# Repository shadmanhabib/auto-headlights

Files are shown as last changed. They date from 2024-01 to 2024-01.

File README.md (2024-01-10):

# Auto-Headlights
Controller designed to control and automate vehicle headlights based on environmental conditions in parallel with vehicle controls.

## Table of Contents
- [Auto-Headlights](#Auto-Headlights)
  - [Table of Contents](#table-of-contents)
  - [About The Project](#about-the-project)
  - [Getting Started](#getting-started)
    - [Prerequisites](#prerequisites)
    - [Installation](#installation)
  - [Usage](#usage)
  - [Changelog](#changelog)

## About The Project
This project was designed for a Subaru Liberty/Legacy 4GEN in an effort to add modern automatic headlights and light home functionalities.

It involves PCB design and automotive wiring. Hence, this project should only be replicated by individuals who are confident with automotive electrical systems.

The design was based around the following requirements:

1. Control headlights dependent on light conditions.
2. Ensure original vehicle controls remained functional.
3. Support reading lock/unlock states.
4. Ability to update software i.e. ensure programing pins are accessible through header/connector.

## Getting Started
To get a build this project (or parts thereof), these steps may be followed.

### Prerequisites
1. PlatformIO is required to build binaries from source code. Microchip Studios or Arduino IDE can also be used but will require extra configuration.
2. An ISP programmer is required to upload to the controller. An Arduino as ISP can be used.
3. If you want to make changes to the PCB design or would like to generate new fabrication files, an installation of KiCAD is required.
4. A 3D printer is required to fabricate the PCB enclosure from the provided CAD files.

### Installation
1. Manufacture and assemble controller PCB.
2. Build and upload code binary.
3. Fabricate PCB enclosure.
4. Splice vehicle wiring as per wiring diragram/requirements.
5. Pin connectors and attach to controller.
6. Mount controller in a secure location.

## Usage
Examples will be given in future iterations of this file.

_For more examples, please refer to the [Documentation](https://)_

## Changelog
All notable changes to this project will be documented in this section.

The format is based on [Keep a Changelog](https://keepachangelog.com/en/1.0.0/),
and this project attempts to adhere to [Semantic Versioning](https://semver.org/spec/v2.0.0.html).

### [v1.0.0]
#### Initial design
- ATmega328PB based design.
- Included optocouplers to read 12V signals from vehicle.
- MOLEX Micro-fit connectors.

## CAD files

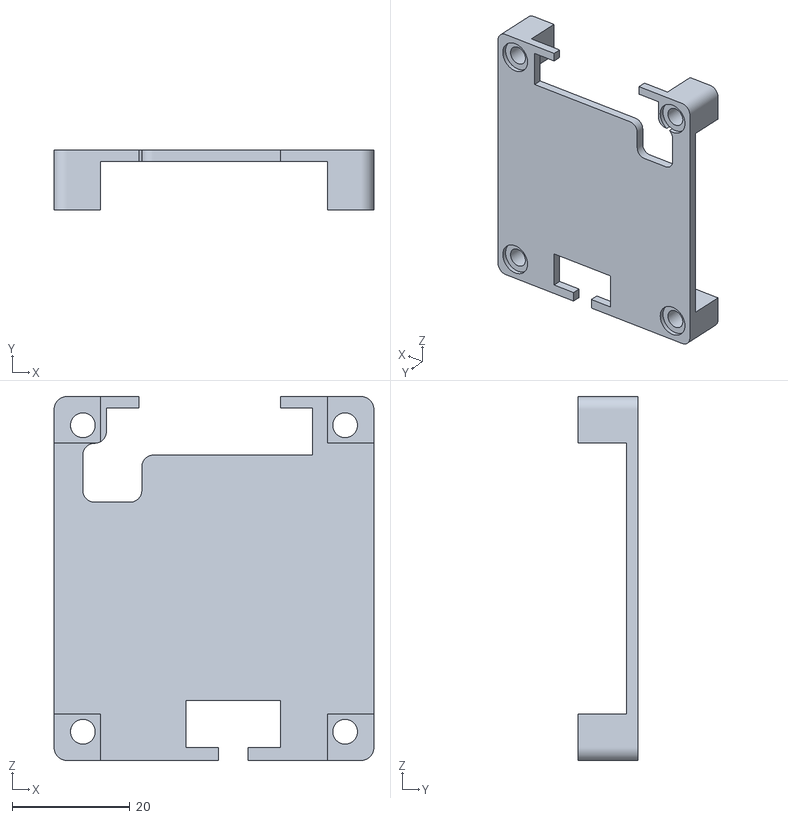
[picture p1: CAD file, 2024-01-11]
CAD/export/lid.obj
54.3 x 10.2 x 61.8

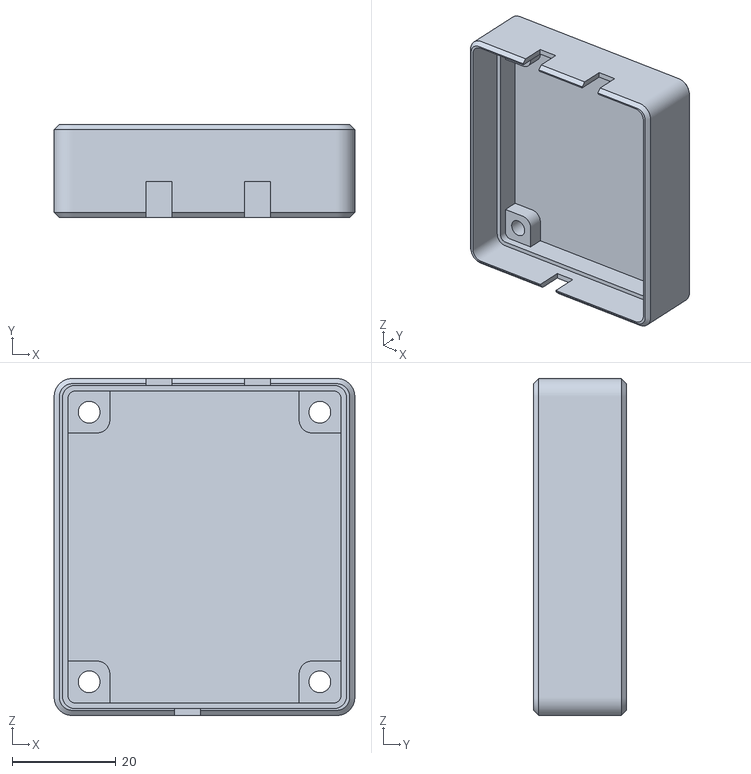
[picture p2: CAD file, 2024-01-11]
CAD/export/case.obj
58.0 x 18.0 x 65.0

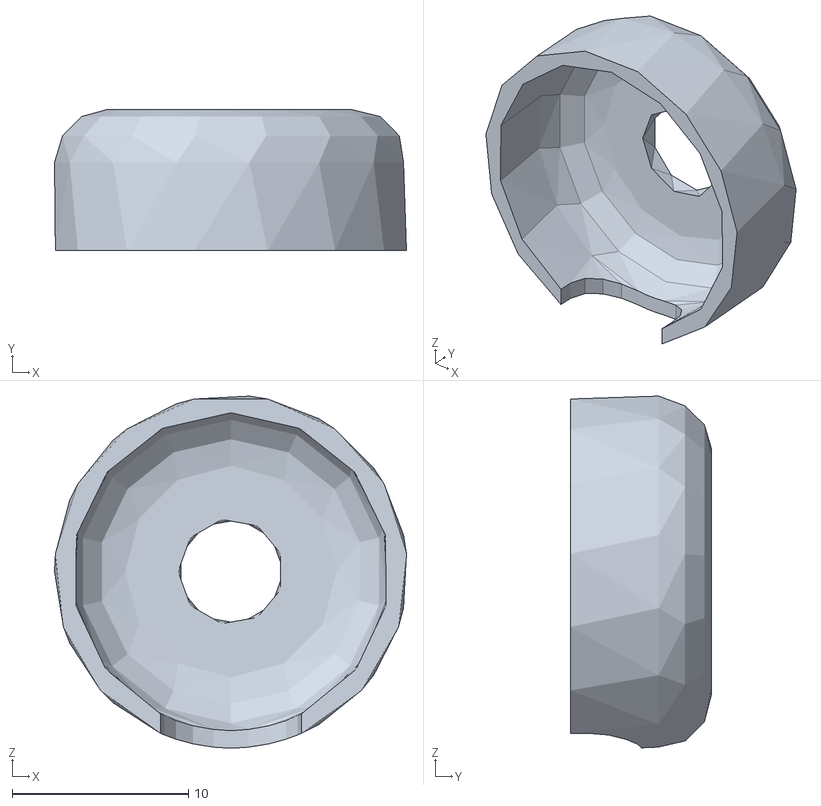
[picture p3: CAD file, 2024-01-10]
CAD/export/Light_sensor_case.obj
19.9 x 8.00 x 19.9

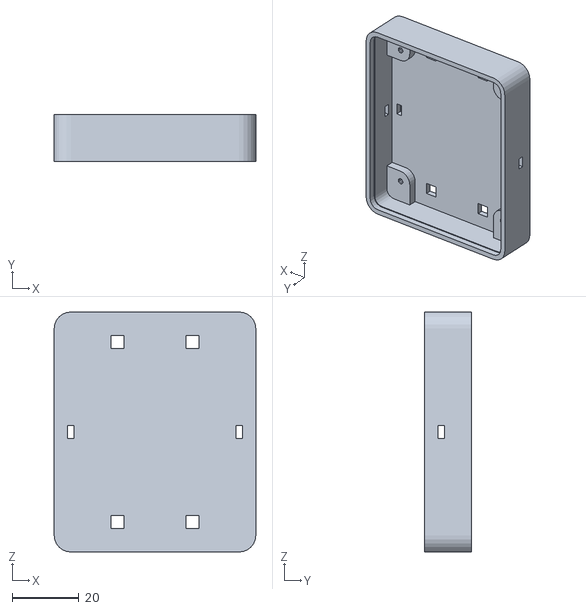
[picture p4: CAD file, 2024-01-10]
CAD/export/PCB_case_1.obj
60.5 x 14.0 x 72.0

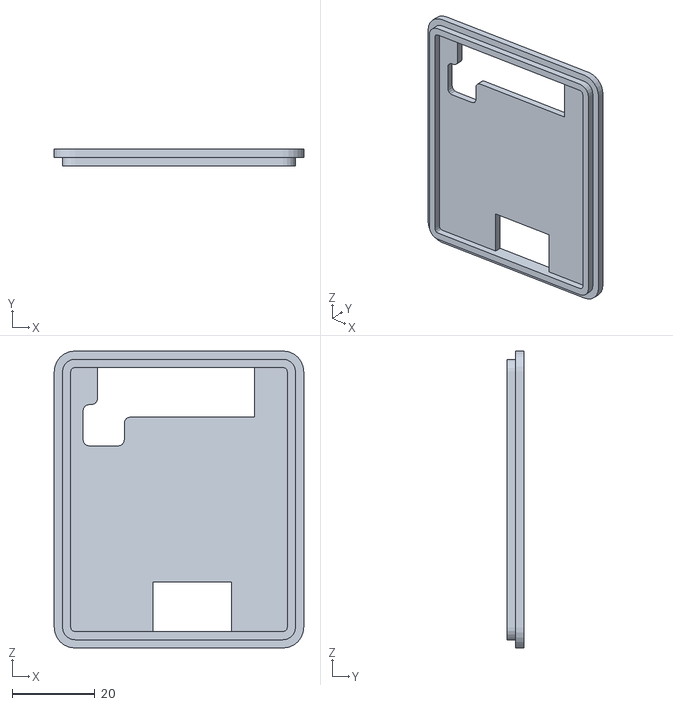
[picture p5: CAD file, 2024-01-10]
CAD/export/PCB_case_2.obj
60.5 x 4.00 x 72.0

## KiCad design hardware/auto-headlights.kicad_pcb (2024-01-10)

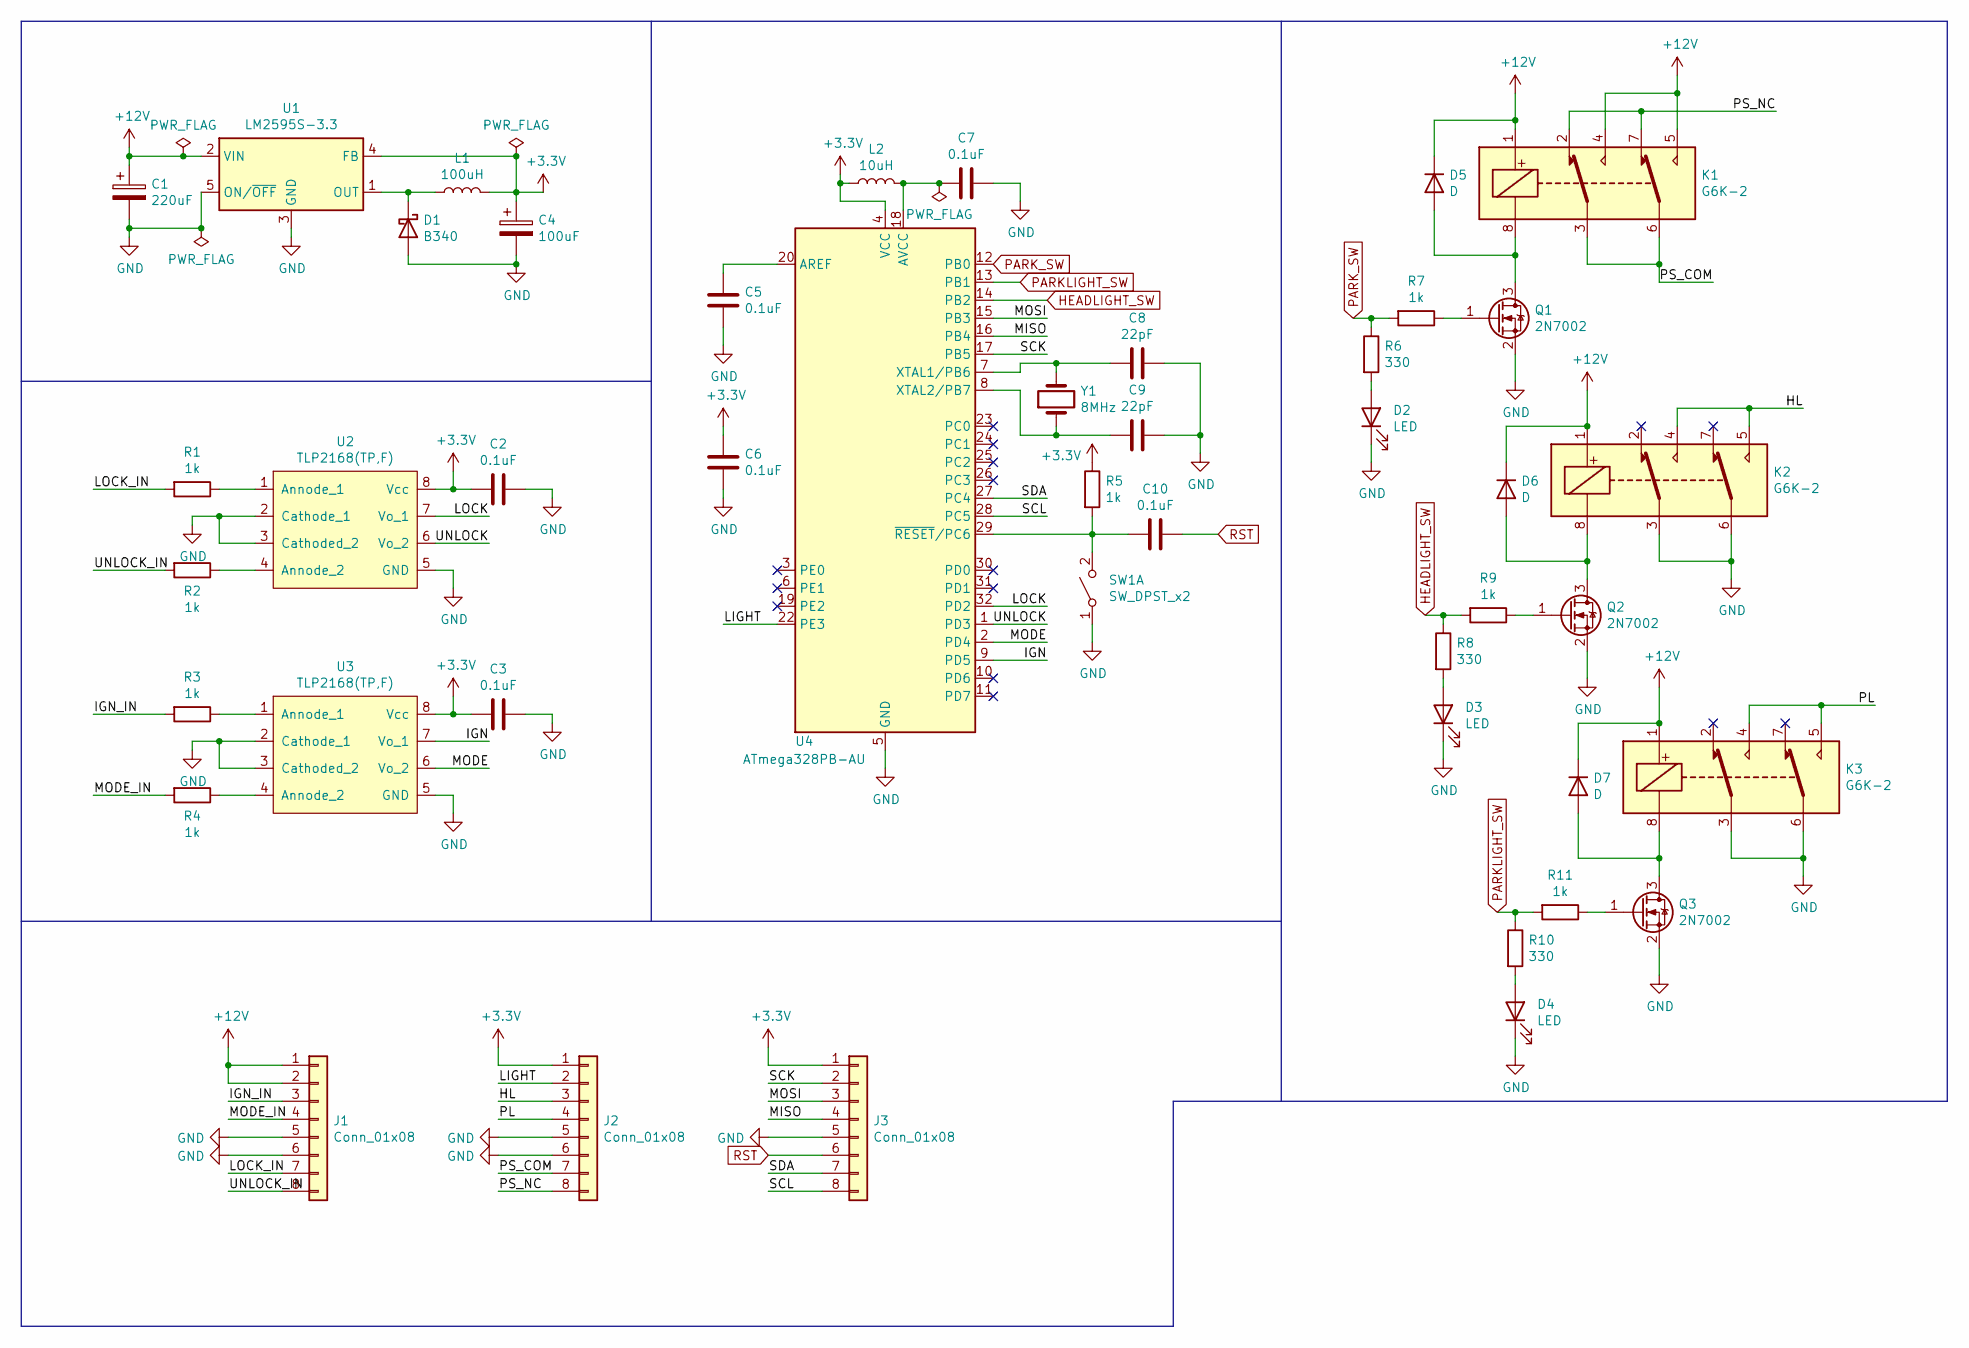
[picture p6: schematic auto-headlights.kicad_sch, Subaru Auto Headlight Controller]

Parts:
C1: 220uF; CP_EIA-7343-31_Kemet-D
C2, C3, C5, C6, C7, C10: 0.1uF; C_0805_2012Metric
C4: 100uF; CP_EIA-3528-21_Kemet-B
C8, C9: 22pF; C_0805_2012Metric
D1: B340; D_SOD-123
D2, D3, D4: LED; LED_0805_2012Metric_Castellated
D5, D6, D7: D; D_SOD-123
J1, J2, J3: Conn_01x08; Molex_Micro-Fit_3.0_43045-0812_2x04_P3.00mm_Vertical
K1, K2, K3: G6K-2; Relay_DPDT_Omron_G6K-2F-Y
L1: 100uH; L_0805_2012Metric
L2: 10uH; L_0805_2012Metric
Q1, Q2, Q3: 2N7002; SOT-23
R1, R2, R3, R4, R5, R7, R9, R11: 1k; R_0805_2012Metric
R6, R8, R10: 330; R_0805_2012Metric
SW1: SW_DPST_x2; SW_SPST_Omron_B3FS-100xP
U1: LM2595S-3.3; TO-263-5_TabPin3
U2, U3: TLP2168(TP,F); SO-8_3.9x4.9mm_P1.27mm
U4: ATmega328PB-AU; TQFP-32_7x7mm_P0.8mm
Y1: 8MHz; Crystal_SMD_5032-2Pin_5.0x3.2mm

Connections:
+3V3: C2.2, C3.2, C4.1, C6.1, J2.1, J3.1, L1.2, L2.1, R5.1, U1.4 (FB), U2.8 (Vcc), U3.8 (Vcc), U4.4 (VCC)
+12V: C1.1, D5.1 (K), D6.1 (K), D7.1 (K), J1.1, J1.2, K1.1, K1.4, K1.5, K2.1, K3.1, U1.2 (VIN)
/HL: J2.3, K2.4, K2.5
/IGN: U3.7 (Vo_1), U4.9 (PD5)
/IGN_IN: J1.3, R3.2
/LIGHT: J2.2, U4.22 (PE3)
/LOCK: U2.7 (Vo_1), U4.32 (PD2)
/LOCK_IN: J1.7, R1.2
/MISO: J3.4, U4.16 (PB4)
/MODE: U3.6 (Vo_2), U4.2 (PD4)
/MODE_IN: J1.4, R4.2
/MOSI: J3.3, U4.15 (PB3)
/PL: J2.4, K3.4, K3.5
/PS_COM: J2.7, K1.3, K1.6
/PS_NC: J2.8, K1.2, K1.7
/SCK: J3.2, U4.17 (PB5)
/SCL: J3.8, U4.28 (PC5)
/SDA: J3.7, U4.27 (PC4)
/UNLOCK: U2.6 (Vo_2), U4.1 (PD3)
/UNLOCK_IN: J1.8, R2.2
GND: C1.2, C2.1, C3.1, C4.2, C5.2, C6.2, C7.1, C8.1, C9.1, D1.2 (A), D2.1 (K), D3.1 (K), D4.1 (K), J1.5, J1.6, J2.5, J2.6, J3.5, K2.3, K2.6, K3.3, K3.6, Q1.2 (S), Q2.2 (S), Q3.2 (S), SW1.1 (A), U1.3 (GND), U1.5 (ON/~OFF), U2.2 (Cathode_1), U2.3 (Cathoded_2), U2.5 (GND), U3.2 (Cathode_1), U3.3 (Cathoded_2), U3.5 (GND), U4.5 (GND), U4.21 (GND)
HEADLIGHT_SW: R8.1, R9.2, U4.14 (PB2)
unnamed: C5.1, U4.20 (AREF)
unnamed: C7.2, L2.2, U4.18 (AVCC)
unnamed: C8.2, U4.7 (XTAL1/PB6), Y1.2
unnamed: C9.2, U4.8 (XTAL2/PB7), Y1.1
unnamed: C10.2, R5.2, SW1.2 (B), U4.29 (~RESET/PC6)
unnamed: D1.1 (K), L1.1, U1.1 (OUT)
unnamed: D2.2 (A), R6.2
unnamed: D3.2 (A), R8.2
unnamed: D4.2 (A), R10.2
unnamed: D5.2 (A), K1.8, Q1.3 (D)
unnamed: D6.2 (A), K2.8, Q2.3 (D)
unnamed: D7.2 (A), K3.8, Q3.3 (D)
unnamed: Q1.1 (G), R7.1
unnamed: Q2.1 (G), R9.1
unnamed: Q3.1 (G), R11.1
unnamed: R1.1, U2.1 (Annode_1)
unnamed: R2.1, U2.4 (Annode_2)
unnamed: R3.1, U3.1 (Annode_1)
unnamed: R4.1, U3.4 (Annode_2)
PARKLIGHT_SW: R10.1, R11.2, U4.13 (PB1)
PARK_SW: R6.1, R7.2, U4.12 (PB0)
RST: C10.1, J3.6

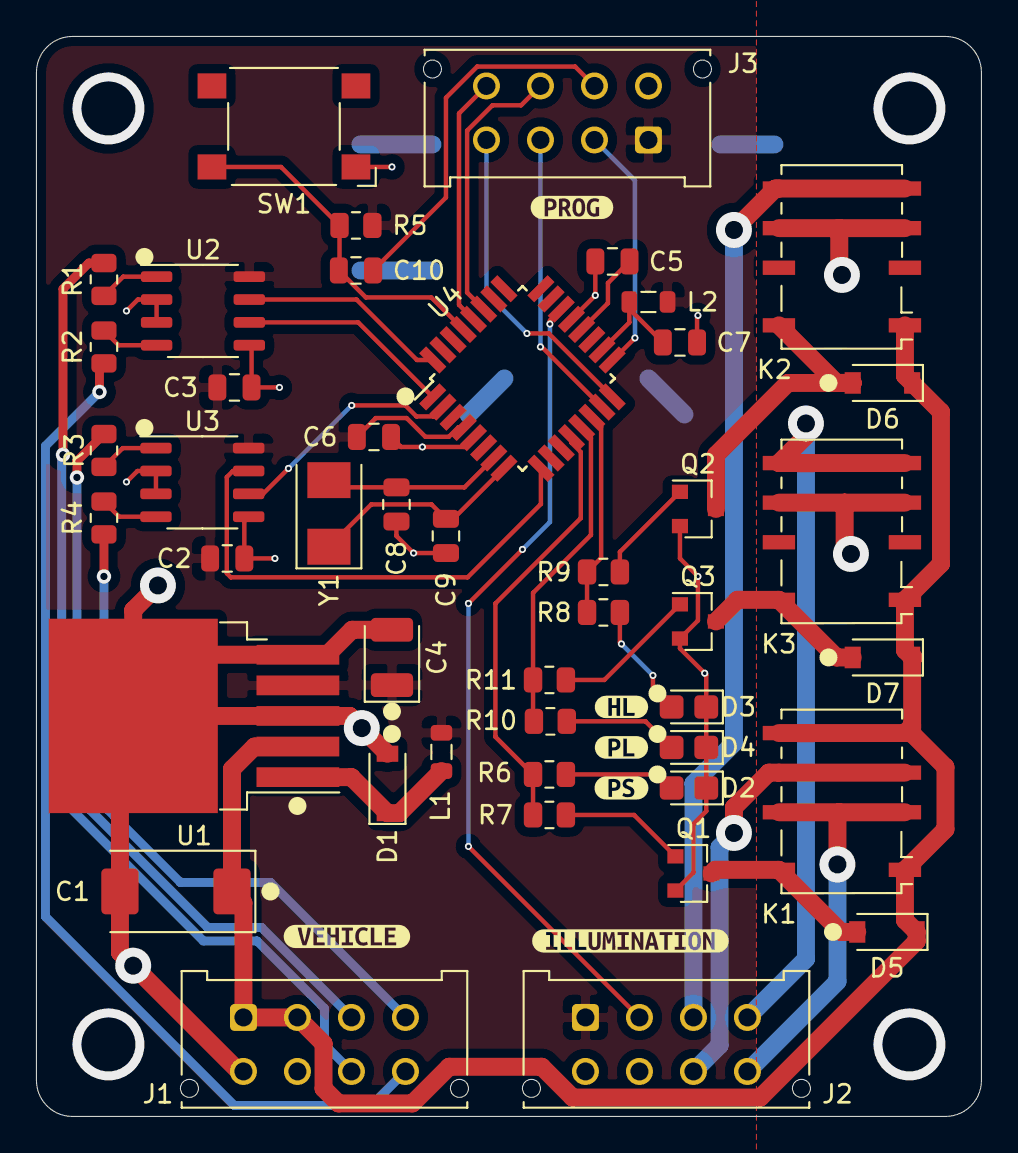
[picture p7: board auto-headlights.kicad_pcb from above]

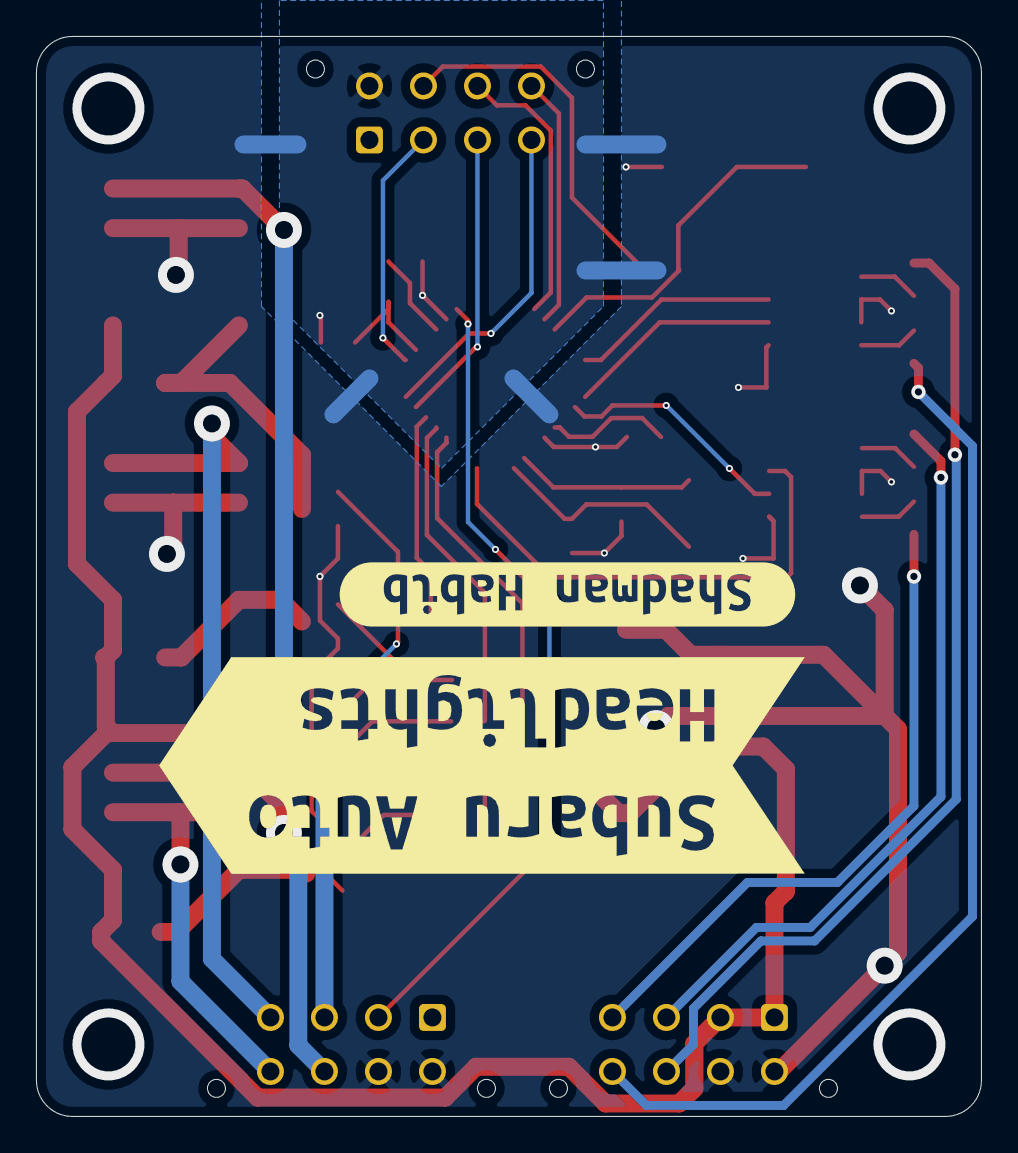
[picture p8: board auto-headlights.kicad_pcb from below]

Board: 2 copper layers, 52.5 x 60.0 mm, 53 parts (2 on the bottom side), 44 nets.

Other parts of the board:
kibuzzard-612DA6C3, kibuzzard-612DA6E7, kibuzzard-612DA7BB, kibuzzard-612DA65A, kibuzzard-612DA66E, kibuzzard-612DA640, kibuzzard-612DA714, kibuzzard-612DA797: G***; label

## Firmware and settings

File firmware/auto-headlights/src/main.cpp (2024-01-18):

/*
 * auto-headlights
 * 
 * Shadman Habib
 * 
 * "main.cpp"
 * Main source file for auto headlight controls on 4GEN Liberty/Legacy vehicles 
 *
 */

#include "header.h"

uint8_t getLights(uint8_t light_bits)  {
  uint8_t aux = light_bits & APARK_MASK;
  light_bits = light_bits >> 1;

  ADCSRA |= (1 << ADSC);
  while ((ADCSRA & 0x40) > 0)  {
    // Wait for ADC conversion to complete
  }

  adcArray[adcIndex] = ADC;
  adcIndex = (adcIndex + 1) % adcSize;

  uint16_t adcSum = 0;
  for (int i = 0; i < adcSize; i++)  {
    adcSum = adcSum + adcArray[i];
  }

  uint16_t adcVal = adcSum / adcSize;

  switch (light_bits)  {
  case 0b00:
    if (adcVal > 600)  {
			light_bits = 0b00;
		} else if (adcVal > 250)  {
			light_bits = 0b01;
		} else  {
			light_bits = 0b11;
		}
    break;
  case 0b01:
    if (adcVal > 800)  {
			light_bits = 0b00;
		} else if (adcVal > 250)  {
			light_bits = 0b01;
		} else  {
			light_bits = 0b11;
		}
    break;
  case 0b11:
    if (adcVal > 800)  {
			light_bits = 0b00;
		} else if (adcVal > 500)  {
			light_bits = 0b01;
		} else  {
			light_bits = 0b11;
		}
    break;
  default:
    light_bits = 0b00;
    break;
  }

  light_bits = (light_bits << 1) | aux;

  return light_bits;
}

SIGNAL (INT0_vect)  {
  // Inturrupt from lock signal
  if (int_timer == 0)  {
    int_timer++;

    if ((state_bits & IGNITION_MASK) == 0)  {
      state_bits |= LOCK_MASK;
      state_bits &= ~APARK_MASK;
      state_bits &= ~LIGHTHOME_MASK;

      // Set output pins for headlights
      LIGHT_PORT = (LIGHT_PORT & ~LIGHT_MASK) | (state_bits & APARK_MASK);
    }
  }
}

SIGNAL (INT1_vect)  {
  // Interrupt from unlock signal
  if (int_timer == 0)  {
    int_timer++;

    if ((state_bits & IGNITION_MASK) == 0)  {
      state_bits &= ~LOCK_MASK;
      _delay_ms(1500);

      if ((state_bits & LIGHT_MASK) > 0)  {
        state_bits |= APARK_MASK;
        state_bits |= LIGHTHOME_MASK;
      }

      // Set output pins for headlights
      LIGHT_PORT = (LIGHT_PORT & ~LIGHT_MASK) | (state_bits & APARK_MASK);
    }
  }
}

SIGNAL (TIMER1_COMPA_vect)  {
  // 100ms state updates
  uint8_t prevState_bits = state_bits;

  state_bits = (state_bits & ~INPUT_MASK) | (~PIND & INPUT_MASK);
  state_bits = (state_bits & ~LIGHT_MASK) | getLights(state_bits & LIGHT_MASK);

  uint8_t changed_states = state_bits ^ prevState_bits;

  // Count for interrupt timer
  if (int_timer != 0)  {
    int_timer = (int_timer + 1) % 20;
  }

  // Turn off light home feature after 1 minute
  // Re-enable auto headlights ater ignition
  if ((state_bits & LIGHTHOME_MASK) > 0)  {
    sw_timer++;

    if (sw_timer >= 250)  {
      state_bits &= ~APARK_MASK;
      state_bits &= ~LIGHTHOME_MASK;
      sw_timer = 0;
    }
  } else if ((state_bits & ENABLE_MASK) == 0)  {
    sw_timer++;

    if (sw_timer >= 25)  {
      state_bits |= ENABLE_MASK;
      sw_timer = 0;
    }
  }

  // Control functions on ignition change
  if ((changed_states & IGNITION_MASK) > 0)  {
    if ((state_bits & IGNITION_MASK) > 0)  {
      state_bits &= ~APARK_MASK;                    // Turn off aux output if ignition turned on
      state_bits &= ~LOCK_MASK;
      state_bits &= ~ENABLE_MASK;
      state_bits &= ~LIGHTHOME_MASK;
    } else if ((state_bits & LIGHT_MASK) > 0)  {
      state_bits |= APARK_MASK;                     // Turn on aux output if ignition turned off and it's dark
      state_bits |= LIGHTHOME_MASK;
    }
    sw_timer = 0;
  }

  // Control function of parking switch and aux output
  if ((state_bits & PARKSW_MASK) > 0)  {
    state_bits |= APARK_MASK;                       // Turn on parking lights with aux output if parking switch is on
  } else if ((prevState_bits & PARKSW_MASK) > 0)  {
    state_bits &= ~APARK_MASK;                      // Turn off aux output if parking switch changes to off
  }

  // Set output pins for headlights
  if ((state_bits & ENABLE_MASK) == 0 || (state_bits & IGNITION_MASK) == 0)  {
    LIGHT_PORT = (LIGHT_PORT & ~LIGHT_MASK) | (state_bits & APARK_MASK);
  } else  {
    LIGHT_PORT = (LIGHT_PORT & ~LIGHT_MASK) | (state_bits & LIGHT_MASK);
  }
}

int main(void)  {
  // Set output pins
  DDRB |= (1 << HEADLIGHT_RELAY) | (1 << PARKING_RELAY) | (1 << AUX_PARK);

	// Set input pins and enable pull-ups
	DDRD &= ~(1 << PARKSW) & ~(1 << IGNITION) & ~(1 << LOCK_SIGNAL) & ~(1 << UNLOCK_SIGNAL);
	PORTD |= (1 << PARKSW) | (1 << IGNITION) | (1 << LOCK_SIGNAL) | (1 << UNLOCK_SIGNAL);

	// Set ADC pin as input
	DDRE &= ~(1 << LIGHT_SENSOR);

  // Set up ADC for light sensor
	ADMUX |= (1 << REFS0) | (1 << MUX2) | (1 << MUX1) | (1 << MUX0);
	ADCSRA |= (1 << ADEN)  | (1 << ADPS2) | (1 << ADPS1) | (1 << ADPS0);

	// Set lock and unlock interrupts
	EICRA |= (1 << ISC01) | (1 << ISC11);
	EIMSK |= (1 << INT0) | (1 << INT1);

  // Set up timers for state and light home feature
	OCR1A  = 3125;						// 100ms equivalent

	TCCR1A = 0x00;						// Set prescaler to 256
	TCCR1B = 0x0C;						// Set mode CTC

	TIMSK1 = 0x02;						// Set inturrupt for OCR1A

  // Enable inturrupts
  sei();

  state_bits |= ENABLE_MASK;

  while (1)  {
    // Controller to run indefinitely
    // Sleep when not working
    SMCR |= (1 << SE);
  }

}

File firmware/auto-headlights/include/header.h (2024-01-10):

/*
 * auto-headlights
 *
 * Shadman Habib
 * 
 * "header.h"
 * Header file containing the required definitions
 * 
 */ 

#include <avr/io.h>
#include <avr/interrupt.h>
#include <stdint.h>
#include <util/delay.h>

// 8 MHz clock
// #define F_CPU				8000000

/*
 * uint8_t state_bits: store vehicle defined states
 * MSB bit 7: enable
 *         6: lock/unlock
 *         5: ignition
 *         4: park switch
 *         3: light home mode on
 *         2: lowbeam on
 *         1: parking on
 * LSB bit 0: aux parking on
 */

uint8_t state_bits = 0b00000000;

// State masks as defined above
#define ENABLE_MASK         0b10000000
#define LOCK_MASK           0b01000000
#define IGNITION_MASK       0b00100000
#define PARKSW_MASK         0b00010000
#define LIGHTHOME_MASK      0b00001000

// Outputs, pin definitions
#define HEADLIGHT_RELAY		PORTB2
#define PARKING_RELAY		PORTB1
#define AUX_PARK			PORTB0

#define LIGHT_PORT		    PORTB
#define LIGHT_MASK          0b00000111
#define APARK_MASK          0b00000001

// Inputs, pin definitions
#define IGNITION			PIND5			// PCINT21
#define PARKSW              PIND4			// PCINT20
#define LIGHT_SENSOR		PINE3
#define LOCK_SIGNAL			PIND2			// INT0
#define UNLOCK_SIGNAL		PIND3			// INT1

#define INPUT_MASK          0b00110000

#define TRUE				1
#define FALSE				0

// ADC Variables
uint8_t adcIndex = 0;
const uint8_t adcSize = 10;
uint16_t adcArray[adcSize] = {0};

// Software counter for time tracking
uint8_t sw_timer = 0;
uint8_t int_timer = 0;

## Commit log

2024-01-06 added hardware and CAD to file structure
2024-01-10 updated interrupt logic and light functions
2024-01-10 import files
    [Light_sensor_case.obj, PCB_case_1.obj, PCB_case_2.obj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]
2024-01-11 Case version 2
    [case.obj, lid.obj]
